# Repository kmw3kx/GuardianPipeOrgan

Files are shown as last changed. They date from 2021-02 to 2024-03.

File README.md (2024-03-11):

# GuardianPipeOrgan

[Terrako by rongs1234 on DeviantArt](https://www.google.com/url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)

## Table of Contents
- [README Requirements](#readme-requirements)
- [Project Pre-Planning](#project-pre-planning)
- [Materials used](#materials-used)
- [Wiring](#wiring)
- [Pseudocode](#pseudocode)
- [Working on the Code](#working-on-the-code)
- [CAD](#cad)
- [Schedule](#schedule)
- [What went wrong](#what-went-wrong)

### README Requirements

<details>
        
        Knock out the design completely in CAD before you start construction.  Leave room for wires.

        Throughout the project, document your work on github.  You should communicate enough information so that someone else in your class could reasonably replicate your project.

        You should include, in this order:

        Description of the planning that went into the project, design decisions, and engineering details
        Materials used
        Wiring diagram of your circuit
        Commented code
        CAD renderings
        Actual photos and/or video (well lit and in focus)
        Your process or a schedule of how you spent your time
        Discussion of problems, errors, miscalculations, and missteps and how you overcame them
        If you didn't finish, please add an obituary, detailing what you'd do if you picked this project back up, and anything you'd have done differently.
        
</details>

### Project Pre-Planning

1. *Create your question:*

  a. *What's the problem you're trying to solve?*

    i. Have a robot that can serenade people with beautiful music
    
    ii. Build a self-playing organ
    
  b. *How will you determine if you've solved your problem? (make sure your problem is specific and testable!)*
  
    i. We can play Zelda's lullaby on it and have it sound pure, and at a constant volume. Is a midi output so that it can also play other songs
    
2. *Break down your problem:*

  a. **Criteria (goals):**
  
    i. *How does it solve the problem?*
    
      1.
      
    ii. *~~What should it look like:~~*
    
    iii. *What is it going to do?*
    
  b. **Constraints (limitations)**
  
    i. *Don't hurt anyone*
    
      1. Pressurized Air can be dangerous
      
    ii. *Budget:*
    
      1. I think we can get by with $50
      
    iii. *Time frame* (roughly 2 months)
    
    iv. *Size* (laser cutter: 300mm x 600mm , 3d Printer 8&quot;x8&quot;x9&quot;)
    
      1. The size that the pipes will need to be
      
    v. *Any knowledge limitations that you'll need to correct?*
    
      1. Pneumatics
      
      2. How to design a valve
      
      3. Controlling multiple solenoids with not many pins
      
      4. Flow rate
      
      5. MIDI Input/Output
      
      6. Organ Pipe design
      
3. *Research:*

  a. *Delegate this with your partner! Whose researching what?*
  
    i. Let's make separate Google Docs to take notes in about each topic
    
      1. Bob = MIDI, Using a microcontroller as a MIDI in/out
      
      2. Justyn = Flow rate, pneumatics, fluid dynamics
      
      3. Both: Organ Pipe Design
      
        a. Hopefully getting in touch with an organ manufacturer up in Staunton
        
  b. *Improve your google-jitsu.*
  
  c. *Remember, you DON'T have a plan yet. This is research for pre-planning. Researching mp3 shields….how does a piezo buzzer work, that sort of thing…WHAT IS PID?? How do I determine CoM in Onshape?*
  
  4. I cannot tell you what questions to ask, as they should be very project specific, but for example, you might want to know how an organ pipe works before building an organ, or you might want to know how to calculate wheel speed , before you build a PID box that controls wheel speed.

4. *Make a list of possible solutions:*

  1. *Whats it going to look like?*

  3. *What components will it use?*

    1. Arduino or Circuit Python
    
  4. *How does this solution solve the problem?*

  6. **Make sure to include a short list of pros and cons for each solution.**

  8.

1. We are pretty decided that it's going to be an organ
2. Solenoids or Solenoid Valves?

  1. Solenoids

    1. Pros: Cheaper, less specialized, have been used before for this type of project

    2. Cons: The solenoid valves are gonna be more precise and a better seal
    
  2. Solenoid valves

    1. Pros
3.

[Link to engineering design process:](https://www.teachengineering.org/design/designprocess)

[Link](https://docs.google.com/document/d/1uND1lurYmUpj-_9FQsYxZuwOPflugXZLaDDHEH4wFzs/edit?usp=sharing)

### Materials used
* 32 Valves (laser-cut casing, [3/16" ID x 5/16" OD silicone tubing](https://www.amazon.com/dp/B07TH8H1QP/ref=cm_sw_em_r_mt_dp_J0TEWZFQ2DN48WCQM4QV?_encoding=UTF8&psc=1), and 3D printed cam)
* 32 3D printed Organ Pipes 
* Arduino Mega (from Dr. Shields)
* [MIDI 5-pin to USB-A Cable](https://www.amazon.com/dp/B087G7L7J2/ref=cm_sw_em_r_mt_dp_3BY1T0T89K53A4C2TZDT?_encoding=UTF8&psc=1)
* [MIDI connector](https://www.amazon.com/dp/B07NY6Z2N7/ref=cm_sw_em_r_mt_dp_BFAF0GJ7GPHXVVTXCVRJ?_encoding=UTF8&psc=1)
* 220 Ohm 1/4watt resistor (In Sigma Lab)
* [1N4148 diode](https://www.amazon.com/dp/B06XB1R2NK/ref=cm_sw_em_r_mt_dp_FQDK5978XHRZRAK23W6Y) (I had one on hand, but I included a link to order one as well)
* 10k Ohm 1/4watt resistor (In Sigma Lab)
* 470 Ohm 1/4watt resistor (I used 2x220 instead)
* [6N138 optocoupler](https://www.amazon.com/dp/B07DLTSXC1/ref=cm_sw_em_r_mt_dp_HDJK9QW9ZMRRCRK7CJNF?_encoding=UTF8&psc=1)
* Balloons!
* Lots of bolts and screws
* Breadboard
* wires

### Wiring

[MIDI Fritzing file](Wiring/MidiCircuit.fzz)

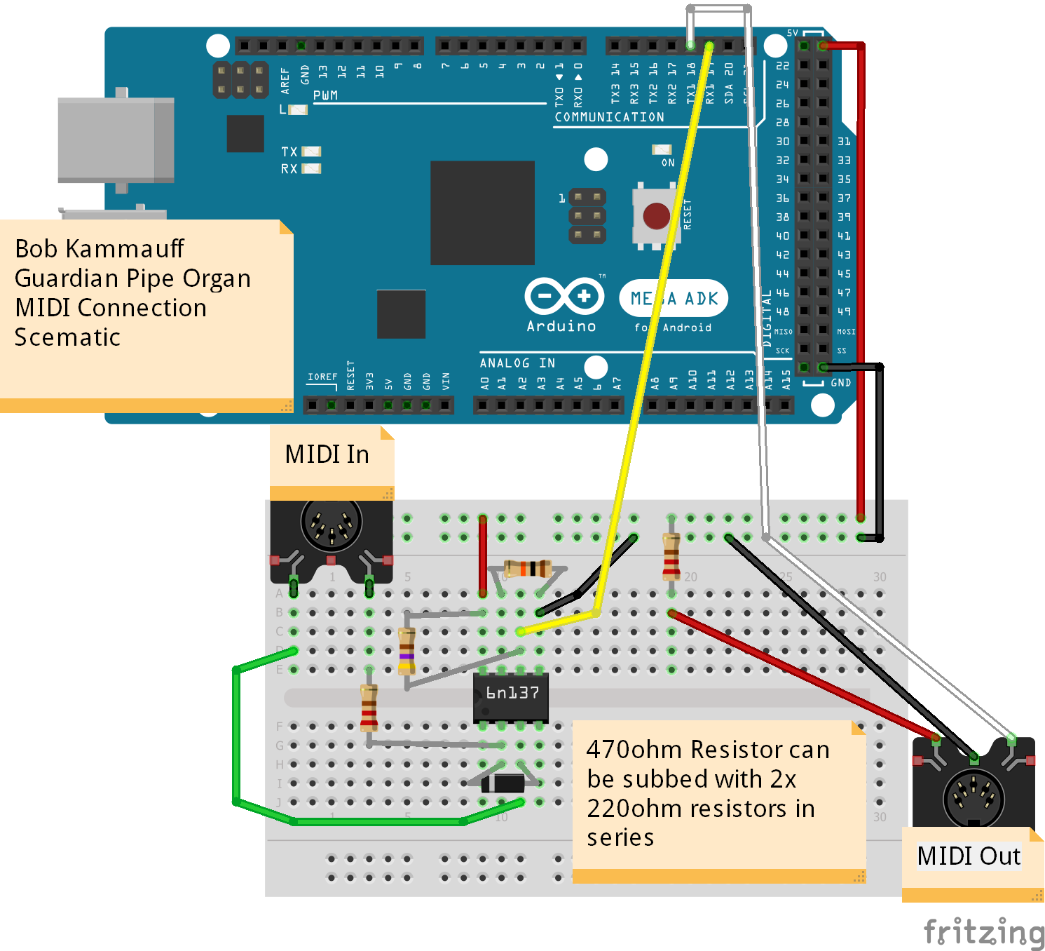
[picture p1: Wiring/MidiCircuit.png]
[](Wiring/MidiCircuit.png)

### Pseudocode
Link to code [here.](GuardianPipeOrganOutPseudoCode)

<details>
        
        ```python
        # Bob Kammauff
        # 2/4/2021
        # Guardian Pipe Organ - Output
        # pseudocode

        # at the top here, put all of the libraries we'll be using

        import time

        import digitalio
        import touchio
        import busio
        import board
        import usb_midi
        import neopixel

        import adafruit_midi

        from adafruit_midi.note_on          import NoteOn
        from adafruit_midi.control_change   import ControlChange
        from adafruit_midi.pitch_bend       import PitchBend

        # + some others that I don't know about

        # set up any serial port communication we'll need

        # using some type of shift register or port thingy to get more pins
        # so initialize that

        # Read any incoming MIDI messages (events) over USB
        # looking for note on, note off messages

        # Our organ will have 32 notes starting at middle C (C4) and going up to G6
        # Each time a note on value is detected, write the pin connected to that note's solonoid high
        # Each time theres a note off value, write the pin low

        # there will be transistors in between every solonoid to supply the correct voltage
        ```
   
</details>

## Working on the Code

Throughout this process, I gradually moved from using multiple metro expresses, to using a metro and an Arduino Mega, to using just the mega. So a lot of what I've written is very specific to the point in time when I was using a metro M0. If you want to read that stuff, I'll include it all into a expanding section:

It's not required for the rest of the README to make sense

<details>

So, I do not have the transistors or the shift registers or any of that fancy stuff yet; all I got is a Circuit Python and some LED's, but the coding will be the same either way. Let's set up a circuit python to read Midi Data coming from my computer to light up some led's.

The wiring is easy. a bunch of LED's and resistors. Iet's get working on the code for it.

Ok so I've already run into a couple problems about how to write the code. The code I'm taking it from sets all of the pins using a for loop. But, I can't find a way to do that with digital pins because they require a 2nd initialization to tell the pin whether to be input or output. Brute forcing it might just be the correct solution, but the idea of having the pins in an array just makes the code so much simpler.

Now that I've described the problem, the solution seems clear: do a mix

This didn't work
        
```python
pins = [board.D13,
        board.D12,
        board.D11,
        board.D10,
        board.D9,
        board.D8,
        board.D7,
        board.D6,
        board.D5,
        board.D4,
        board.D3,
        board.D2]

# add LED's
# ledG = digitalio.DigitalInOut(board.D1)
# ledG.direction = digitalio.Direction.OUTPUT
# n
# or do it like this

noteLEDs = []
x = 0
for pin in pins:
    noteLEDs = [digitalio.DigitalInOut(pin)]
    print(str(pin))

del pins, x  # done with that
noteLEDs.direction = digitalio.Direction.OUTPUT
```

Lets try this now: set the pins each to a variable, then set each variable to a list.

```python
pinD13 = digitalio.DigitalInOut(board.D13)
pinD12 = digitalio.DigitalInOut(board.D12)
pinD11 = digitalio.DigitalInOut(board.D11)
pinD10 = digitalio.DigitalInOut(board.D10)
pinD9 = digitalio.DigitalInOut(board.D9)
pinD8 = digitalio.DigitalInOut(board.D8)
pinD7 = digitalio.DigitalInOut(board.D7)
pinD6 = digitalio.DigitalInOut(board.D6)
pinD5 = digitalio.DigitalInOut(board.D5)
pinD4 = digitalio.DigitalInOut(board.D4)
pinD3 = digitalio.DigitalInOut(board.D3)
pinD2 = digitalio.DigitalInOut(board.D2)

pinD13.direction = digitalio.Direction.OUTPUT
pinD12.direction = digitalio.Direction.OUTPUT
pinD11.direction = digitalio.Direction.OUTPUT
pinD10.direction = digitalio.Direction.OUTPUT
pinD9.direction = digitalio.Direction.OUTPUT
pinD8.direction = digitalio.Direction.OUTPUT
pinD7.direction = digitalio.Direction.OUTPUT
pinD6.direction = digitalio.Direction.OUTPUT
pinD5.direction = digitalio.Direction.OUTPUT
pinD4.direction = digitalio.Direction.OUTPUT
pinD3.direction = digitalio.Direction.OUTPUT
pinD2.direction = digitalio.Direction.OUTPUT

noteLEDs = [pinD13,
            pinD12,
            pinD11,
            pinD10,
            pinD9,
            pinD8,
            pinD7,
            pinD6,
            pinD5,
            pinD4,
            pinD3,
            pinD2]

# Brute forced
```
</details>

Anyway, here's my thought process simplified:

After trying to get serial communication working with a metro express and failing for a week, I decided to totally ditch using one and instead use just an arduino mega to process MIDI data and control all of the servos. 

This means that instead of being able to send midi data just across the usb cable like with the metro, I actually had to go and order a MIDI to USB cable from Amazon. [Here's](https://www.amazon.com/dp/B087G7L7J2/ref=cm_sw_em_r_mt_dp_3BY1T0T89K53A4C2TZDT?_encoding=UTF8&psc=1) the one I ended up buying.

I guess I should explain my goals for this code:

1. Connect the arduino mega to the 32 servos that control the valves
2. Receive data being transmitted over the MIDI IN jack hooked up to the computer
3. process that data to get what note should be either turned on or off
4. send the corresponding command to the servo, allowing air to pass, and make the organ pipe speak.

[Here's](https://github.com/jkammau97/GuardianPipeOrgan/blob/8430313b24fd7d28eb77173dfa6983c463fdca4e/Arduino%20Code/GuardianPipeOrganV1/GuardianPipeOrganV1.ino) the code I came up with for the servos:

<details>
        ```arduino
        
        /*
          Bob Kammauff & Justyn Reyes
          Midi Output - Guardian Pipe Organ
          3/25
          Last Updated: 5/24/2021
        */

        #include <Servo.h>
        #include <stdio.h>
        #include <string.h>

        #define NUM_NOTES 32
        #define FIRST_PIN 22
        Servo servos[NUM_NOTES];

        #define OFF_ANGLE 0
        #define ON_ANGLE 180

        #define FIRST_NOTE 53 //corresponds to F3
        #define LAST_NOTE 84 //corresponds to C6

        //If input falls outside this range, data gets thrown out

        int note, velocity;

        String fromSerial;

        char input[10];

        int incomingByte = 0; // for incoming serial data

        void setup() {
          // put your setup code here, to run once:
          Serial.begin(9600); //For communicating with the computer

          for (int i = 0; i < NUM_NOTES; i++)
          {
            servos[i].attach(i + FIRST_PIN);

            Serial.print("Servo ");
            Serial.print(i);
            Serial.print(" attached to pin ");
            Serial.println(i + FIRST_PIN);
            servos[i].write(OFF_ANGLE);

          }
          Serial.println("All Servos Attached");

          for (int n = 0; n < NUM_NOTES; n++)
          {
            Serial.print("Testing servo ");
            Serial.println(n);
            servos[n].write(ON_ANGLE);
            delay(100);
            servos[n].write(OFF_ANGLE);
            delay(50);
          }

          Serial.println("Done");
        }

        void loop() {
          // put your main code here, to run repeatedly:
          // send data only when you receive data:
          while (Serial.available() > 0)
          {
            fromSerial = Serial.readStringUntil('\n');
            Serial.println(fromSerial); //Echoes back what was received
            fromSerial.toCharArray(input, fromSerial.length());
            // Returns first token
            char *token = strtok(input, " ");
            note = atoi(token);
            token = strtok(NULL, " ");
            velocity = atoi(token);
            // Keep printing tokens while one of the
            // delimiters present in str[].
            if (note >= FIRST_NOTE and note <= LAST_NOTE) //If note is in range
            {
              Serial.print("Note is: ");
              Serial.println(note, DEC);
              Serial.print("Vel is: ");
              Serial.println(velocity, DEC);
              if (velocity > 0)
              {
                servos[note - FIRST_NOTE].write(ON_ANGLE);
              } else
              {
                servos[note - FIRST_NOTE].write(OFF_ANGLE);
              }

            }

          }
        }
        
        ```
</details>

This code simply establishes communication with the servos, and ties each one to a note. In MIDI, each note on the keyboard is assigned a name and an integer corresponing to said note, and then the next part of the data packet the midi sends over is called velocity, which is simply how loud the note should be played. I'll include some specifics about how a midi byte is transferred in the section about the midi code, but for now, all you need to know is that midi data simply sends over a note and whether to turn it on or off at the time when it is sent. So, back when I had no access to said midi data, I made up my own and simply sent it over the serial monitor from my computer. The syntax for said data is: note integer, space, velocity integer(anything that wasn't zero turned it on, with zero turning it off), and another space. My code takes that data, splits it via the spaces, and then converts the text of the numbers into actual integer values that it can use in calculations. These values are then echoed back over the serial monitor, and the corresponding servo makes the correct movement. 
        
Now, for the MIDI code that reads the data coming over the ports! [Here](Arduino Code/ReceiveMidiWEdits/ReceiveMidiWEdits.ino) it is!

I'm actually going to wait to put it in the README for now. It needs a LOT of polishing up, but this is the source that I got it from, and where I'm going to continue to work on this code
        
This code DOES work and it works consistently, but it's not giving me the data that I was expecting it to. It's like a geode; the gem I'm looking for is in there, but it's gonna take some parsing to extract it into a useable chunk. instead of giving me `command, note, velocity` like I was expecting, it's giving me: `Command byte, 255, 255, Note byte, 255, 255, Velocity byte, 255, 255`

### CAD

[Link to Onshape](https://cvilleschools.onshape.com/documents/e358e4e3ba9e07c5ae938246/w/c6c09eac29318e33af1bc1ef/e/29cbd6e08dd43a0f8d613074)
        
The majority of this project was spent in CAD HELL. Trying to make a 3D object that converts air into sound is challenging to get right. What I first ended up doing was researching how Pipe organ pipes make sound and what kind of geometry creates said conditions. 
        
I'm especially proud of my design for the pipes. They are stopped organ pipes with caps to adjust the tuning. Stopping the organ pipes drops the octave and requires less air pressure to sound, allowing for them to be more practical in my design. They are as thin walled as i could 3D print. 
        
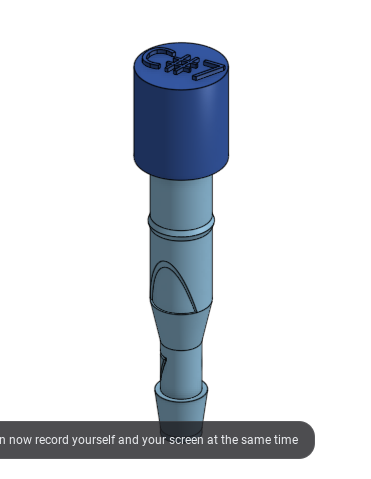
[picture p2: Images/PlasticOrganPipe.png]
[](Images/PlasticOrganPipe.png)
        
I filled in the space under the top lip to allow these organ pipes to be able to be printed with no supports! Carefully follow the slope and cut it off with a razor blade and it should work perfectly. Be careful with the bottom lip; if it gets too mangled, it might not direct air towards the upper lip and the organ pipe won't sound.
        
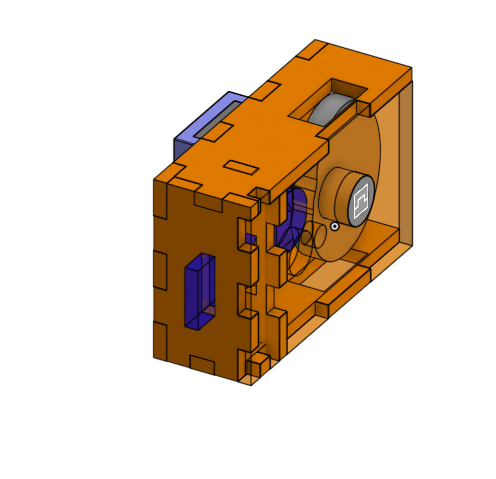
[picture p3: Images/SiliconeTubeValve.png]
[](Images/SiliconeTubeValve.png)

I am also very proud of the valve design. They use silicone tubing and a mini servo in a cam and follower mechanism to stop air flow electronically, much cheaper than a solenoid valve. The design is not my own (I can't find the original inspiration, sadly), but I did increase the size to accomodate a higher volume of air.

### Schedule

| 1st week |  Get midi working with the circuit pythons  |  Feb. 22nd-26th |
|:---:|:---:|:---:|
| 2nd week | Order all of the parts we’ll need | Mar. 1st-5th |
| 3rd week | Design the organ pipes and the valve system | Mar. 8th-12th |
| 4th week | Design the Shell to put the organ into | Mar. 15th-19th  |
| 5th week | Fabrication | Mar.22nd-26th |
| 6th week | Troubleshooting (buffer week) | Mar. 29th-Apr.2 |

#### 3rd Week

Bob Goal: Finish the design for the organ pipes. Design the Valve system.

Justyn Goal: Fix up the github, Add pictures, cad, toc. Lay out the valves once Bob Has made the valves

Evaluation: Bob really had trouble delegating work, so we only achieved designing the valve system. We finally our 3D printed Whistle prototype and that has caused us to reevaluate the design of our organ. Instead of using open flue organ pipes, we are going to use closed organ flue pipes, because they allow for a lower tone in a smaller size, and require less air pressure. And we are going to do pipes C5-G7 so they are smaller yet (longest one is 1/2 a foot!) Since they are now smaller, the silicone tubing of 1/4" might be too big now, which means we'll have to redesign the valve to fit the new size of tubing.

#### 4th Week
Justyn: Design the Organ pipes to make them stopped and tune-able by adjusting the screw on stopper. Add nozzle on the bottom to directly friction fit connect the tubes to. add brackets to the design of the organ pipes to hold them upright

Bob: Work on code; Get Servos working with midi and arduino mega.

3/17/2021

Justyn is having computer problems so I'm the only one who can do Onshape. I had to really think about how big everything was going to be, so I had to scale it down to the bottom note of F4 instead of C5. Really, I just couldn't realistically fabrcate pipes smaller than that C7 stopped pipe. I added threads on to both the cap and the top of the pipe so that the pipes can be tuned relatively easily. Hopefully. Next course of action is to define the silicone tubing size again and then remake the valve so it is smaller. Lot's of redesigning, but it will all work out.

#### 5th Week

Ok so thankfully, at the time I am writing this, my life has just gotten way less busy. All of my music stuff is done, so it's time to focus on school again. But we're also super behind on schedule. Today, I just realized that there was an extremely simple solution to this project: buy a cheap melodica and put it in the guardian. Unfortunately, we're already so deep into the organ pipes that it's pointless to just start from scratch, and besides; I prefer the flute tone of the pipes instead of the reedy tone of te melodica. That, and that the melodica wouldn't fit nicely in the robot. but that's an easy idea to save for the future!

This week, Bob is on code, and Justyn is on CAD. Thankfully, I think most of the code for the arduino mega is already on the internet so I can just borrow it. But first, we need to establish a tubing size, and then 

### What Went Wrong

Why will I be unable to finish this project by the end of the year? A few reasons:

1. Lack of In-Person Lab time with my partner
2. Long turn-around on fabrication
3. The project is just insane

#### 1. Lack of In-Person Lab time with my partner

Never being able to actually see my partner face to face makes it extremely difficult to collaborate. I would try to delegate work for him to do but not being able to see him doing it and making sure he stayed on track meant that I would ultimately be the one doing it. Me also being the only one to understand the physics of sound and midi also meant it was challenging to convey what I wanted. 

I could fix this in the future by not choosing such a complicated project to do during a national pandemic. Also I started to remedy the problem by coming in on my virtual days when we started having school in person. 

#### 2. Long turn-around on fabrication

This started with me 3D printing the first test whistle. It easily took 2 weeks from submitting the file for printing to actually get it into my hands so I could test it. That day I learned the hard lesson to never print a closed cyllender. To quote my teach: 
> "closed or nearly closed cylinders are nightmares, filled with monsters and support material that wont dissolve."

This was just the starting point of design hell. Trying to print something that makes sound is incredibly difficult, because you just can't see how it will sound in CAD; you have to print it out and test it.

Thankfully I did my research and found out how whistles make noise so there was less of that, but I still had to print out 5 separate pipes before one of them actually worked. When ur not in the lab 5 days a week, it just increases the turn-around time as it would have to dissolve in the bath for at least a day after printing

The circumstances aren't just to blame; I also had to learn how to design parts that would use no support material. I did a good job with it tho, cuz my parts are now real nice.

#### 3. The project is just insane

When I was first pitching it to my teacher, he thought I just wanted to make a robot play music, so he suggested that I just use a MP3 shield and call it a day 

**Oh how easy that would've been...**

MIDI-Controlled Pipe Organs are just so cool. Something about bringing the perfection of MIDI into the physical world just sounds so cool when you hear it. But it's also just unlike anything anyone else here has tried to do, so I have to build it from the ground up. Thankfully there are projects online that are quite similar, but I was still just trying to figure out the best way to do it only a month ago. 

        I hope to revisit this project someday, but for the time being, it'll have to wait.

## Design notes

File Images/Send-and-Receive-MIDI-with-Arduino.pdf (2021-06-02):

## http://www.instructables.com/id/Send-and-Receive-MIDI-with-Arduino/

Food (http://www.instructables.com/tag/type-id/category-food/) Living (http://www.instructables.com/tag/type-id/category-living/) Outside (http://www.instructables.com/tag/type-id/category-outside/) | Play (http://www.instructables.com/tag/type-id/category-play/) | Technology (http://www.instructables.com/tag/type-id/category-technology/) Workshop (http://www.instructables.com/tag/type-id/category-workshop/)

# Send and Receive MIDI with Arduino

by amandaghassaei (http://www.instructables.com/member/amandaghassaei/?utm_source=pdf&utm_campaign=title) on June 9, 2012

## Table of Contents

## Author:amandaghassaei amandaghassaei.com Currently working for instructables!

# Intro: Send and Receive MIDI with Arduino

This instructable will show you how to use an Arduino to send and receive a variety of MIDI messages so you can start building your own MIDI controllers and instruments. First I'll talk a little bit about MIDI protocol, if you're just looking for sample code skip ahead to steps 5-9.

If you know absolutely nothing about MIDI note, velocity, and pitchbend or are confused about what MIDI does and why you would want to use it, check out my What is MIDI? (http://www.instructables.com/id/What-is-MIDI/) instructable.

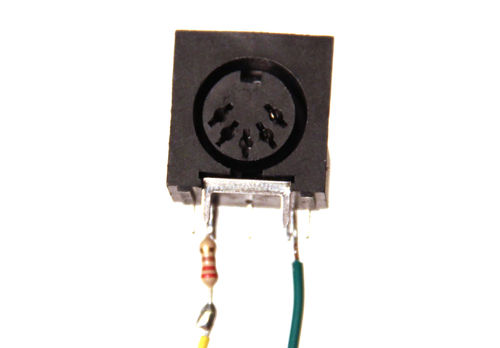
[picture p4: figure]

# Step 1: Bytes and Bits

To understand MIDI communication, you have to understand a little about bytes and bits. A byte is a packet of data used to store information. In MIDI protocol, each byte

## is made up of 8 bits; bits can only equal to 0 or 1. A sample byte is given below:

11010111

Each 1 or 0 in this byte is a bit. The leftmost bit is called the most significant bit (or MSB) and the rightmost bit is called the least significant bit (or LSB).

Bytes of the form above are binary numbers because they are expressed using only 1's and 0's. We can convert this number to base ten as well:

## 11010111 in binary (base 2) = 215 in decimal (base 10)

If you need help converting numbers from binary to decimal or vice versa check out Wolfram Alpha (http://www.wolframalpha.com/) . Type in a binary number followed with "from binary to decimal" to get the decimal equivalent. Wolfram Alpha is also great for converting to and from hexadecimal (http://en.wikipedia.org/wiki/Hexadecimal) .

Wikipedia is a good resource for more information about bytes (http://en.wikipedia.org/wiki/Byte) and binary (http://en.wikipedia.org/wiki/Binary_numeral_system) .

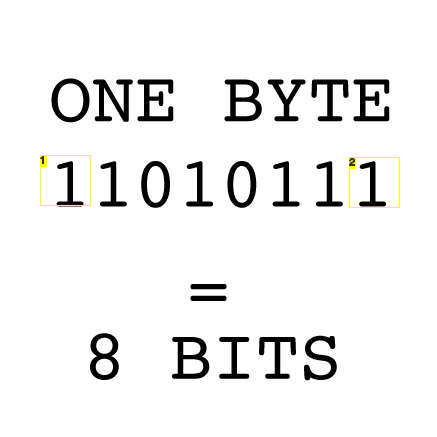
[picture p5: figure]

## Image Notes 1. most significant bit (MSB) 2. least significant bit (LSB)

# Step 2: A Bit About MIDI Protocol

A really basic overview of MIDI terms and concepts is given here (http://www.instructables.com/id/What-is-MIDI/) .

MIDI messages are comprised of two components: commands and data bytes. The command byte tells the MIDI instrument what type of message is being sent and the subsequent data byte(s) store the actual data. For example a command byte might tell a MIDI instrument that it going to send information about pitchbend, and the data byte describes how much pitchbend and which note to pitchbend.

MIDI data bytes range from 0 to 127. Convert these numbers to binary and we see they range from 00000000 to 01111111, the important thing to notice here is that they always start with a 0 as the most significant bit (MSB). MIDI command bytes range from 128 to 255, or 1000000 to 11111111 in binary. Unlike data bytes, MIDI command bytes always start with a 1 as the MSB. This MSB is how a MIDI instrument differentiates between a command byte and a data byte.

## MIDI commands are further broken down by the following system:

The first half of the MIDI command byte (the three bits following the MSB) sets the type of command. More info about the meaning on each of these commands is here (http://www.instructables.com/id/What-is-MIDI/) .

## 10000000 = note off 10010000 = note on 10100000 = aftertouch 10110000 = continuous controller 11000000 = patch change 11010000 = channel pressure 11100000 = pitch bend 11110000 = non-musical commands

The last half of the command byte sets the MIDI channel. All the bytes listed above would be in channel 0, command bytes ending in 0001 would be for MIDI channel 1, and so on.

All MIDI messages start with a command byte, some messages contain one data byte, others contain two or more (see image above). For example, a note on command byte is followed by two data bytes: note and velocity.

I'm going to explain how to use note on, note off, velocity, and pitchbend in this instructable, since these are the most commonly used commands. I'm sure you will be able to infer how to set up the others by the end of this.

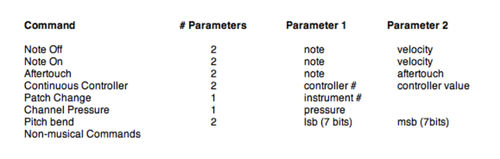
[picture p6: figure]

# Step 3: Send MIDI Messages with Arduino- Hardware

## Parts List:

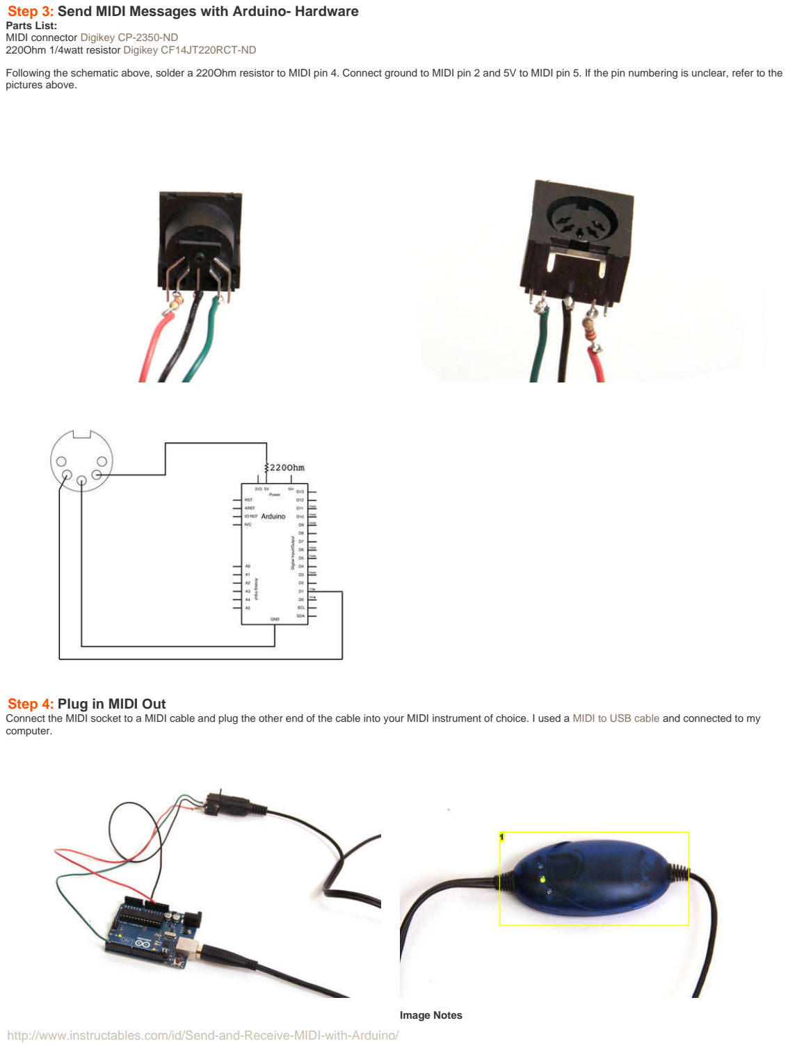
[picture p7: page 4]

MIDI connector Digikey CP-2350-ND (http://www.digikey.com/product-detail/en/SDS-50J/CP-2350-ND/97033)
220Ohm 1/4watt resistor Digikey CF14JT220RCT-ND (http://www.digikey.com/product-detail/en/CF14JT220R/CF14JT220RCT-ND/1830334)

Following the schematic above, solder a 220Ohm resistor to MIDI pin 4. Connect ground to MIDI pin 2 and 5V to MIDI pin 5. If the pin numbering is unclear, refer to the pictures above.

# Step 4: Plug in MIDI Out

Connect the MIDI socket to a MIDI cable and plug the other end of the cable into your MIDI instrument of choice. I used a MIDI to USB cable (http://www.amazon.com/Cable-Converter-Music-Keyboard-Window/dp/B0017H4EBG) and connected to my computer.

## Image Notes

## 1. MIDI to usb

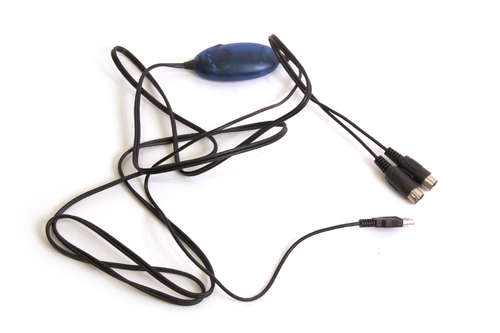
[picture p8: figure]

# Step 5: Basic Note On, Note Off with Arduino

This code sends MIDI messages out arduino digital pin 1 using note on and note off commands.

## As I explained in step 3, the MIDI commands for note on and note off are as follows: noteON = 10010000 = 144 noteOFF = 10000000 = 128

Both of these commands are followed by two more bytes to make a complete MIDI message, the first is note and the second is velocity (for more info about what "note" and "velocity" mean check out my introductory MIDI instructable). Note and velocity can range from 0 to 127. In this example I used notes ranging from 50 to 69 (D3 to A4):

## for (int note=50;note<70;note++){} and I set the velocity to 100:

int velocity = 100;

So when the function MIDImessage() is called in the loop() of the arduino sketch, it sends the three bytes: Serial.write(command);
Serial.write(MIDInote);
Serial.write(MIDIvelocity);
if the "command" in the MIDImessage() function is noteON then the note will start, if it is noteOFF the note will stop.

The code below plays the notes D3-A4 in a loop, it turns on a MIDI note for 300ms then wait 200ms before turning on the next note. I wrote a MaxMSP (http://cycling74.com/downloads/) patch (you can download the runtime version for free) that displays the incoming MIDI messages and attached it below. Here is an example video:

/*
MIDI On/Off Messages
By Amanda Ghassaei
July 2012
http://www.instructables.com/id/Send-and-Receive-MIDI-with-Arduino/

* This program is free software; you can redistribute it and/or modify * it under the terms of the GNU General Public License as published by * the Free Software Foundation; either version 3 of the License, or * (at your option) any later version.

*/

int vel = 100;//velocity of MIDI notes, must be between 0 and 127 //higher velocity usually makes MIDI instruments louder

int noteON = 144;//144 = 1001000 in binary, note on command
int noteOFF = 128;//128 = 10000000 in binary, note off command

void setup() {
// Set MIDI baud rate:
Serial.begin(31250);
}

void loop() {
for (int note=50;note<70;note++) {//from note 50 (D3) to note 69 (A4) MIDInoteON(note, vel);//turn note on
delay(300);//hold note for 300ms
MIDInoteOFF(note, vel);//turn note off
delay(200);//wait 200ms until triggering next note }
}

//send MIDI message- turn note on
void MIDInoteON(int pitch, int velocity) { Serial.write(noteON);//send note on command Serial.write(pitch);//send pitch data Serial.write(velocity);//send velocity data }

//send MIDI message- turn note off
void MIDInoteOFF(int pitch, int velocity) { Serial.write(noteOFF);//send note off command Serial.write(pitch);//send pitch data Serial.write(velocity);//send velocity data }

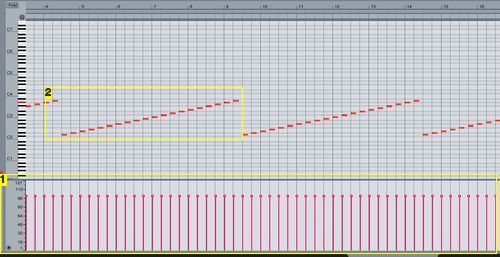
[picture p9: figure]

## Image Notes 1. velocity set to constant 100 2. 20 notes, increasing by one semitone, with .3s duration

## File Downloads

midiin.maxpat.zip (http://www.instructables.com/files/orig/FK2/FFFM/H673DC2U/FK2FFFMH673DC2U.zip) (1 KB)
[NOTE: When saving, if you see .tmp as the file ext, rename it to 'midiin.maxpat.zip'] (http://www.instructables.com/files/orig/FK2/FFFM/H673DC2U/FK2FFFMH673DC2U.zip)

# Step 6: Note Off with 0 Velocity

You may have noticed in the previous step's video, that the velocity appeared to set back to 0 when the note off message was sent. This is because a MIDI message with a note on command and velocity 0 is the same as a note off message. Sometimes when a software MIDI environment receives a note off message it will automatically translate it into a note on message with velocity 0 because they are the same. You will probably find that it is easier to program MIDI by sending these note on/velocity=0 messages rather than sending note off.

The code below does the exact same thing as the code in the last step, but it only uses note on commands. Essentially, I've replaced the following line: MIDImessage(noteOFF, note, velocity);

## with:

MIDImessage(noteON, note, 0);

/*
MIDI On Messages with 0 velocity
By Amanda Ghassaei
July 2012
http://www.instructables.com/id/Send-and-Receive-MIDI-with-Arduino/

* This program is free software; you can redistribute it and/or modify * it under the terms of the GNU General Public License as published by * the Free Software Foundation; either version 3 of the License, or * (at your option) any later version.

*/

int velocity = 100;//velocity of MIDI notes, must be between 0 and 127 //(higher velocity usually makes MIDI instruments louder)

int noteON = 144;//144 = 1001000 in binary, note on command

void setup() {
// Set MIDI baud rate:
Serial.begin(31250);
}

void loop() {
for (int note=50;note<70;note++) {//from note 50 (D3) to note 69 (A4) MIDImessage(noteON, note, velocity);//turn note on delay(300);//hold note for 300ms
MIDImessage(noteON, note, 0);//turn note off
delay(200);//wait 200ms until triggering next note }
}

//send MIDI message
void MIDImessage(int command, int MIDInote, int MIDIvelocity) { Serial.write(command);//send note on or note off command Serial.write(MIDInote);//send pitch data Serial.write(MIDIvelocity);//send velocity data
}

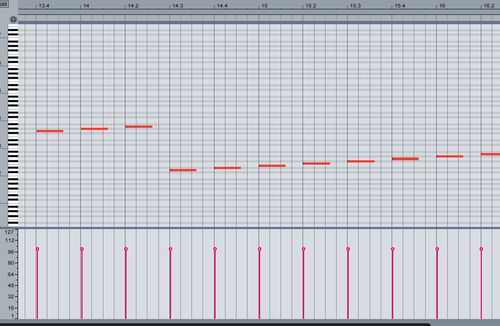
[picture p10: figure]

# Step 7: Variable Velocity and Arduino

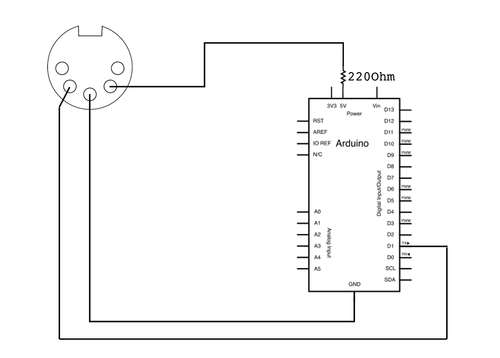
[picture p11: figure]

In this code I've modified the variable velocity so that it increases with increasing note number. In the beginning of the loop() function the variable velocity is set to 20,

## then it is increased by five in each iteration of the for loop:

velocity += 5;
so for note = 50, velocity = 20, then for note = 51, velocity = 25, then for note = 52, velocity = 30... and so on.
once the end of the loop() function is reached, the velocity is reset back to 20.

Here's a video of the end result, notice how the volume increases with increasing velocity.

/*
MIDI note on messages with variable velocity
By Amanda Ghassaei
July 2012
http://www.instructables.com/id/Send-and-Receive-MIDI-with-Arduino/

* This program is free software; you can redistribute it and/or modify * it under the terms of the GNU General Public License as published by * the Free Software Foundation; either version 3 of the License, or * (at your option) any later version.

*/

int noteON = 144;//144 = 1001000 in binary, note on command

void setup() {
// Set MIDI baud rate:
Serial.begin(31250);
}

void loop() {
int velocity = 20;//set velocity to 20
for (int note=50;note<70;note++) {//from note 50 (D3) to note 69 (A4) MIDImessage(noteON, note, velocity);//turn note on delay(300);//hold note for 300ms
MIDImessage(noteON, note, 0);//turn note off
delay(200);//wait 200ms until triggering next note velocity += 5;//ad 5 to current velocity value
}

//send MIDI message
void MIDImessage(int command, int MIDInote, int MIDIvelocity) {

Serial.write(command);//send note on or note off command Serial.write(MIDInote);//send pitch data Serial.write(MIDIvelocity);//send velocity data

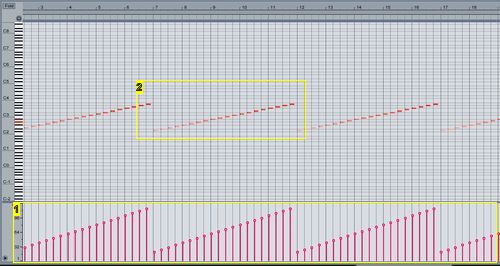
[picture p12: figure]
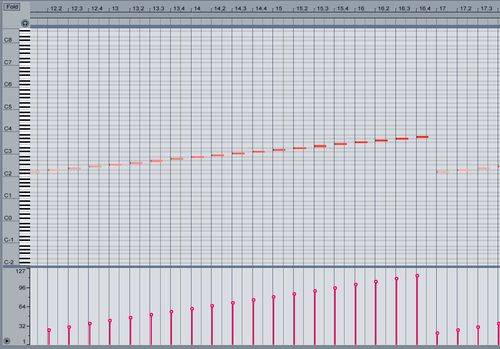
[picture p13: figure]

## Image Notes 1. velocity increases by 5 2. 20 notes, increasing by one semitone, duration of 0.3s

# Step 8: Pitchbend and Arduino

Now that you know how to control note on and note off, you can try pitchbend.

Pitchbend information is stored in 2 data bytes, and most significant byte (MSB) and a least significant byte (LSB). Each of these bytes contains only 7 bits of information. This means that all pitchbend information is stored in 14 bits, with the most significant 7 bits stored in the MSB and the least significant 7 bits stored in the LSB.

For most applications you will only find yourself changing pitchbend via the MSB and just setting the LSB to 0. In this case you have 7 bits of resolution for pitchbend (128 steps). In MIDI protocol pitchbend = 64 is no pitchbend, pitchbend greater than 64 is pitchbends the frequency up, and less than 64 pitchbends the frequency down.

In the example below a note played and held, then played again while the pitchbend increments from 64 to its max value of 127, then played a third time while the pitchbend increments from 64 to its min value of 0. This sequence is looped forever. The images above show the output in ableton from this Arduino sketch.

/*
MIDI Pitchbend (msb)
By Amanda Ghassaei
July 2012
http://www.instructables.com/id/Send-and-Receive-MIDI-with-Arduino/

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

*/

int noteON = 144;//144 = 1001000 in binary, note on command
//noteON data storage:
int note = 60;//middle c
int velocity = 100;//velocity of MIDI notes, must be between 0 and 127 //(higher velocity usually makes MIDI instruments louder)

int pitchbend = 224;//224 = 11100000 in binary, pitchbend command //pitchbend data storage:
int lsb = 0;//least siginificant bit of pitchbend message
int msb = 0;//most significant bit of pitchbend message

void setup() {
// Set MIDI baud rate:
Serial.begin(31250);

void loop() {
//first play note w/o pitchbend
MIDImessage(pitchbend, 0, 64);//reset pitchbend to 0 (zero pitchbend is lsb = 0, msb = 64) MIDImessage(noteON, note, velocity);//turn note on
delay(700);//sustain note
MIDImessage(noteON, note, 0);//turn note off
delay(500);//wait 500ms until triggering next note

//then play with pitchbend up
MIDImessage(pitchbend, 0, 64);//reset pitchbend to 0 (zero pitchbend is lsb = 0, msb = 64) MIDImessage(noteON, note, velocity);//turn note on
for (msb=64;msb<=127;msb++){//increase pitchbend msb 64 (no pitchbend) to 127 MIDImessage(pitchbend, lsb, msb);//send pitchbend message
delay(10);
}
MIDImessage(noteON, note, 0);//turn note off
delay(500);//wait 500ms until triggering next note

//then play with pitchbend down
MIDImessage(pitchbend, 0, 64);//reset pitchbend to 0 (zero pitchbend is lsb = 0, msb = 64) MIDImessage(noteON, note, velocity);//turn note on
for (msb=64;msb>=0;msb--){//decrease pitchbend msb from 64 (no pitchbend) to 0; MIDImessage(pitchbend, lsb, msb);//send pitchbend message
delay(10);
}
MIDImessage(noteON, note, 0);//turn note off delay(500);//wait 200ms until triggering next note }

//send MIDI message
void MIDImessage(int command, int data1, int data2) { Serial.write(command);//send command byte Serial.write(data1);//send data byte #1 Serial.write(data2);//send data byte #2
}

Below is a video demonstration of the code above. For this piece of code, pitchbend will be most noticeable in instruments with a long sustain, such as a string instrument, keep that in mind when testing the code for yourself.

You will most likely be fine using only 128 steps of pitchbend resolution, but in case you must use all 16384 steps, see the code below. Basically what I've done here is defined a variable called pitchbendVal, which varies from 0 to 16383. As I said below the "zero" pitchbend value is msb = 64 and lsb = 0. In binary this is:

## MSB = 64 = 01000000 LSB = 0 = 0000000 (remember MSB and LSB are 7 bit numbers)

## putting these values together we get:

1000000 0000000

## MSB LSB

or

10000000000000

## which translates to 8192 in decimal

so now the "zero" pitchbend value is 8192.

You'll also notice I had to break the variable pitchbendVal into two 7 bit parts to send out via MIDI message: MIDImessage(pitchbend, (pitchbendVal&27), (pitchbendVal>>7));

## the first part, pitchbendVal&127, returns the least significant 7 bits of pitchbendVal the second part, pitchbendVal>>7, returns the most significant 7 bits of pitchbendVal

see & (http://arduino.cc/en/Reference/BitwiseAnd) and >> (http://arduino.cc/en/Reference/Bitshift) on the Arduino reference page for more info.

/*
MIDI Pitchbend (full resolution)
By Amanda Ghassaei
July 2012
http://www.instructables.com/id/Send-and-Receive-MIDI-with-Arduino/

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

*/

int noteON = 144;//144 = 1001000 in binary, note on command
//noteON data storage:
int note = 60;//middle c
int velocity = 100;//velocity of MIDI notes, must be between 0 and 127 //(higher velocity usually makes MIDI instruments louder)

int pitchbend = 224;//224 = 11100000 in binary, pitchbend command //pitchbend data storage:
int pitchbendVal = 8192;//value between 0 and 16383. zero pitchbend = 8192

void setup() {
// Set MIDI baud rate:
Serial.begin(31250);
}

void loop() {
//first play note w/o pitchbend
pitchbendVal = 8192;//reset pitchbend to "0" (zero pitchbend is pitchbendVal = 8192) MIDImessage(pitchbend, (pitchbendVal&27), (pitchbendVal>>7));//send pitchbend message MIDImessage(noteON, note, velocity);//turn note on
delay(700);//sustain note
MIDImessage(noteON, note, 0);//turn note off
delay(500);//wait 500ms until triggering next note

//then play with pitchbend up
pitchbendVal = 8192;//reset pitchbend to "0" (zero pitchbend is pitchbendVal = 8192) MIDImessage(pitchbend, (pitchbendVal&27), (pitchbendVal>>7));//send pitchbend message MIDImessage(noteON, note, velocity);//turn note on
for (pitchbendVal=8192;pitchbendVal<16384;pitchbendVal++){//increase pitchbend from 8192 to 16383 MIDImessage(pitchbend, (pitchbendVal&27), (pitchbendVal>>7));//send pitchbend message delay(1);
}
MIDImessage(noteON, note, 0);//turn note off
delay(500);//wait 500ms until triggering next note

//then play with pitchbend down
pitchbendVal = 8192;//reset pitchbend to "0" (zero pitchbend is pitchbendVal = 8192) MIDImessage(pitchbend, (pitchbendVal&27), (pitchbendVal>>7));//send pitchbend message MIDImessage(noteON, note, velocity);//turn note on
for (pitchbendVal=8192;pitchbendVal>=0;pitchbendVal--){//decrease pitchbend 8192 to 0; MIDImessage(pitchbend, (pitchbendVal&27), (pitchbendVal>>7));//send pitchbend message delay(1);
}
MIDImessage(noteON, note, 0);//turn note off
delay(500);//wait 500ms until triggering next note }

//send MIDI message
void MIDImessage(int command, int data1, int data2) { Serial.write(command);//send command byte Serial.write(data1);//send data byte #1 Serial.write(data2);//send data byte #2
}

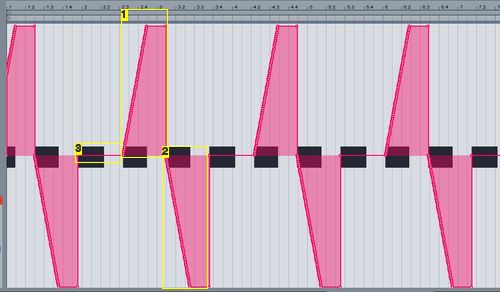
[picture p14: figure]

## Image Notes 1. pitchbend increments up from 0 to max 2. pitchbend increments down from 0 to min 3. constant pitchbend of 64 = no pitchbend

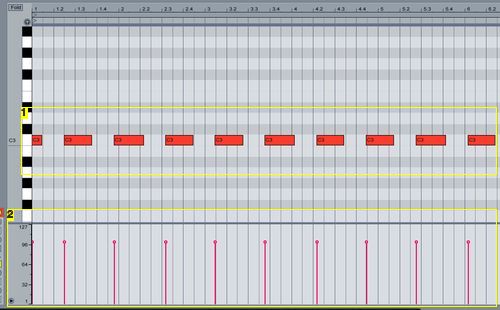
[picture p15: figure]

## Image Notes 1. same note (middle c) repeated over and over 2. constant velocity

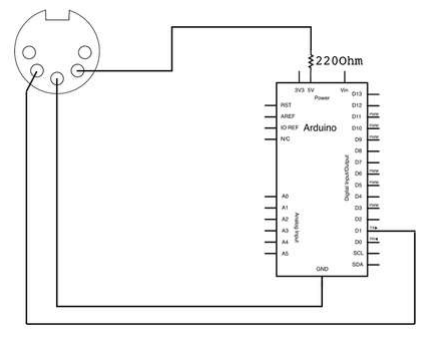
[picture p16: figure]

# Step 9: Receive MIDI Messages with Arduino

Most Arduino MIDI projects send MIDI messages out, but you can also use the Arduino to receive MIDI data. Here are some ideas:

## an Arduino synthesizer that uses MIDI messages to construct audio waveforms

a device which uses MIDI to trigger mechanical events, like the ringing of different sized bells

## a MIDI to control voltage(CV) device- communication between MIDI and analog synthesizers

## Parts List:

MIDI connector Digikey CP-2350-ND (http://www.digikey.com/product-detail/en/SDS-50J/CP-2350-ND/97033)
220Ohm 1/4watt resistor Digikey CF14JT220RCT-ND (http://www.digikey.com/product-detail/en/CF14JT220R/CF14JT220RCT-ND/1830334)
1N4148 diode Digikey1N4148-TAPCT-ND (http://www.digikey.com/product-detail/en/1N4148-TAP/1N4148-TAPCT-ND/3104296)
10kOhm 1/4watt resistor Digikey CF14JT10K0CT-ND (http://www.digikey.com/product-detail/en/CF14JT10K0/CF14JT10K0CT-ND/1830374)
470 Ohm 1/4watt resistor Digikey CF14JT470RCT-ND (http://www.digikey.com/product-detail/en/CF14JT470R/CF14JT470RCT-ND/1830342) (I used 2x220 instead)
6N138 optocoupler Digikey 751-1263-5-ND (http://www.digikey.com/product-detail/en/6N138/751-1263-5-ND/1731496)

The hardware setup is slightly more complicated for receiving MIDI than it is for sending. As you can see in the schematic above, you have to set up an optoisolator in between the MIDI jack and the Arduino. If you are confused about the MIDI pin connections, refer to fig 1. I set this circuit up on a breadboard in figs 4 and 5.

The following code receives these messages, reads them, and stores them appropriately. See the comments for more information.

/*Receive Midi
By Amanda Ghassaei
July 2012
http://www.instructables.com/id/Send-and-Receive-MIDI-with-Arduino/

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

*/

byte commandByte;
byte noteByte;
byte velocityByte;

void setup(){
Serial.begin(31250);
}

void checkMIDI(){
do{
if (Serial.available()){
commandByte = Serial.read();//read first byte noteByte = Serial.read();//read next byte velocityByte = Serial.read();//read final byte
}
}
while (Serial.available() > 24);//when three bytes available }

void loop(){
checkMIDI();
}
To make sure that everything is working properly, try the code below. This code turns the led at pin 13 on briefly when it receives a note on message for MIDI note 60 (middle C). Notice how I included "& velocityByte>0" in the if statement- this makes sure that we are dealing with a note on statement, if you don't include this the light will blink for both note on and note on with velocity = 0 (note off) messages.

/*Receive MIDI and check if note = 60
By Amanda Ghassaei
July 2012

* This program is free software; you can redistribute it and/or modify

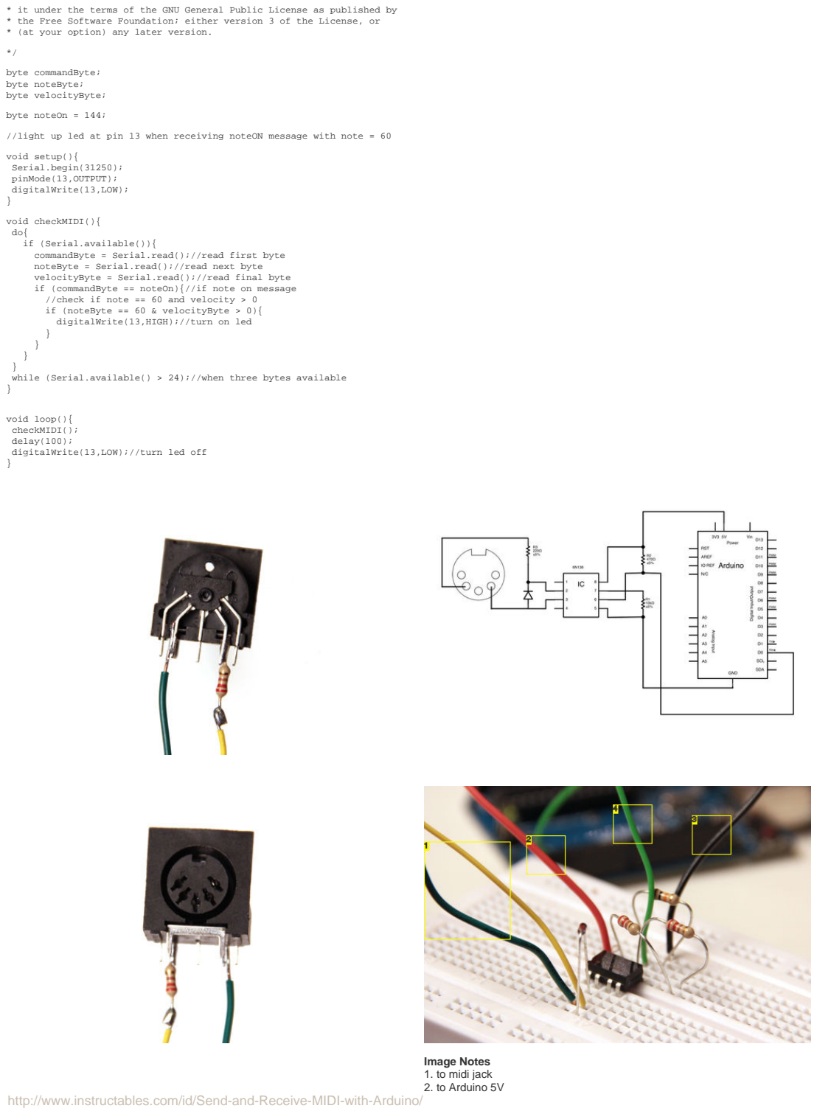
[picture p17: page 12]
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

*/

byte commandByte;
byte noteByte;
byte velocityByte;

byte noteOn = 144;

//light up led at pin 13 when receiving noteON message with note = 60

void setup(){
Serial.begin(31250);
pinMode(13,OUTPUT);
digitalWrite(13,LOW);
}

void checkMIDI(){
do{
if (Serial.available()){
commandByte = Serial.read();//read first byte noteByte = Serial.read();//read next byte velocityByte = Serial.read();//read final byte if (commandByte == noteOn){//if note on message //check if note == 60 and velocity > 0
if (noteByte == 60 & velocityByte > 0){ digitalWrite(13,HIGH);//turn on led
}
}
}
}
while (Serial.available() > 24);//when three bytes available }

void loop(){
checkMIDI();
delay(100);
digitalWrite(13,LOW);//turn led off }

## Image Notes 1. to midi jack 2. to Arduino 5V

## 3. to Arduino ground 4. to RX (digital pin 0)

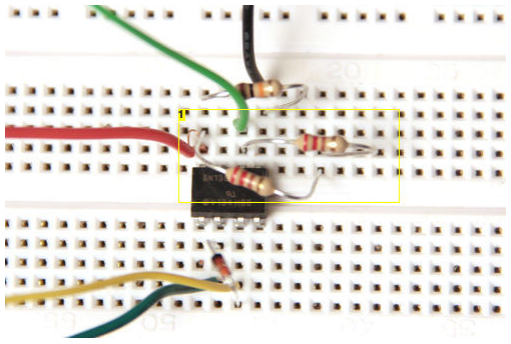
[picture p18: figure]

## Image Notes

1. I used two 220ohm resistors instead of one 470ohm.

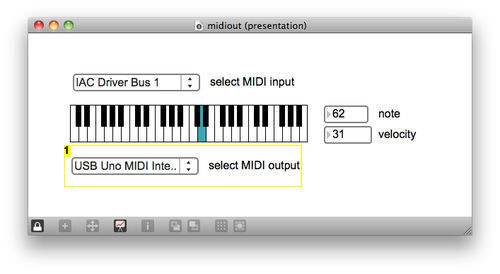
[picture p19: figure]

## Image Notes 1. select Arduino here

## File Downloads

midiout.maxpat.zip (http://www.instructables.com/files/orig/FJ9/A58S/H6DWVEBU/FJ9A58SH6DWVEBU.zip) (1 KB)
[NOTE: When saving, if you see .tmp as the file ext, rename it to 'midiout.maxpat.zip'] (http://www.instructables.com/files/orig/FJ9/A58S/H6DWVEBU/FJ9A58SH6DWVEBU.zip)

# Step 10: Examples

I recently built a MIDI controller with a built in accelerometer and gyroscope (http://www.instructables.com/id/Use-an-Accelerometer-and-Gyroscope-with-Arduino/) , as well as 16 backlit buttons. I'll be posting the full project soon (still need to finish enclosure and a few other things), but I've attached some example code that shows how I got the MIDI up and running. Here is a video of two programs I've written so far:

## And here is the code for those applications:

## single pixel moving around, triggering MIDI (only uses x and y accelerometer):

//accelerometer test- single pixel
//by Amanda Ghassaei 2012
//http://www.instructables.com/id/Send-and-Receive-MIDI-with-Arduino/

/*
* This program is free software; you can redistribute it and/or modify * it under the terms of the GNU General Public License as published by * the Free Software Foundation; either version 2 of the License, or * (at your option) any later version.
*
*/

//pin connections
//#define ledLatchPin 6
//#define ledClockPin 5
//#define ledDataPin 7
//#define buttonLatchPin 4
//#define buttonClockPin 3
//#define buttonDataPin 2

//setup varibles for Gyroscope/Accelerometer int xGyroRAW;
int yGyroRAW;
int xAccRAW;
int yAccRAW;
int zAccRAW;

byte xGyro;
byte yGyro;
byte xAcc;
byte yAcc;
byte zAcc;

//looping variables
byte i;
byte j;
byte k;

//storage for led states, 4 bytes byte ledData[] = {0, 0, 0, 0}; //storage for buttons, 4 bytes byte buttonCurrent[] = {0,0,0,0}; byte buttonLast[] = {0,0,0,0};

byte buttonEvent[] = {0,0,0,0}; byte buttonState[] = {0,0,0,0};
//button debounce counter- 16 bytes
byte buttonDebounceCounter[4][4];

//variables for accelerometer pixel movement boolean firstPress = 1;
byte movingPixel[] = {0, 0, 0, 0};
byte yPosition;
byte xPosition;
int timeX = 0;
int timeY = 0;
boolean dirX = 0;
boolean dirY = 0;
byte lastX = 4;
byte lastY = 4;

//MIDI variables
int velocity = 100;
int noteON = 144;
int MIDIoffset = 60;
byte currentX;

void setup() {

DDRD = 0xFA;//set pins D7-D4 as output, D2 as input

Serial.begin(31250);//MIDI baud rate
// Serial.begin(9600);

cli();//stop interrupts

//set timer1 interrupt at 1kHz
TCCR1A = 0;// set entire TCCR1A register to 0 TCCR1B = 0;// same for TCCR1B
TCNT1 = 0;//initialize counter value to 0; // set timer count for 1khz increments
OCR1A = 1999;// = (16*10^6) / (1000*8) - 1 // turn on CTC mode
TCCR1B |= (1 << WGM12);
// Set CS11 bit for 8 prescaler
TCCR1B |= (1 << CS11);
// enable timer compare interrupt TIMSK1 |= (1 << OCIE1A);

sei();//allow interrupts

}

ISR(TIMER1_COMPA_vect) {//Interrupt at freq of 1kHz timeX++;//increment timeX
timeY++;//increment timeY
shift();//send data to leds
}

// buttonCheck - checks the state of a given button.
//this buttoncheck function is largely copied from the monome 40h firmware by brian crabtree and joe lake
void buttonCheck(byte row, byte index)
{
if (((buttonCurrent[row] ^ buttonLast[row]) &(1 << index)) && // if the current physical button state is different from the ((buttonCurrent[row] ^ buttonState[row]) &(1 << index))) { // last physical button state AND the current debounced state
if (buttonCurrent[row] &(1 << index)) { | // if the current physical button state is depressed
buttonEvent[row] = 1 << index; | // queue up a new button event immediately
buttonState[row] |= (1 << index); | // and set the debounced state to down.
}
else{
buttonDebounceCounter[row][index] = 12;
} // otherwise the button was previously depressed and now
// has been released so we set our debounce counter.
}
else if (((buttonCurrent[row] ^ buttonLast[row]) &(1 << index)) == 0 && // if the current physical button state is the same as
(buttonCurrent[row] ^ buttonState[row]) &(1 << index)) { | // the last physical button state but the current physical
// button state is different from the current debounce
// state...
if (buttonDebounceCounter[row][index] > 0 && --buttonDebounceCounter[row][index] == 0) { // if the the debounce counter has // been decremented to 0 (meaning the
// the button has been up for
// kButtonUpDefaultDebounceCount
// iterations///
buttonEvent[row] = 1 << index; | // queue up a button state change event
if (buttonCurrent[row] &(1 << index)){ | // and toggle the buttons debounce state.
buttonState[row] |= (1 << index);
}
else{
buttonState[row] & ~(1 << index); }
}
}
}

void shift(){

for (i=0;i<4;i++){

buttonLast[i] = buttonCurrent[i];

byte dataToSend = (1 << (i+4)) | (15 &~ledData[i]);

// set latch pin low so the LEDs don't change while sending in bits PORTD&B10111111;//digitalWrite(ledLatchPin, LOW);
// shift out the bits of dataToSend
//shiftOut(ledDataPin, ledClockPin, LSBFIRST, dataToSend);
for (j=0;j<8;j++){
PORTD&B11011111;//digitalWrite(ledClockPin,LOW); //digitalWrite(ledDataPin,((dataToSend>>j)&));
if ((dataToSend>>j)&1){
PORTD|=B10000000;
}
else{
PORTD&B01111111;
}
PORTD|=B00100000;//digitalWrite(ledClockPin,HIGH); }
//set latch pin high so the LEDs will receive new data PORTD|=B01000000;//digitalWrite(ledLatchPin, HIGH);

// SlowDown is put in here to waste a little time while we wait for the state of the output // pins to settle. Without this time wasting loop, a single button press would show up as // two presses (the button and its neighbour)
volatile int SlowDown = 0;

while (SlowDown < 15)
{
SlowDown++;
}

//once one row has been set high, receive data from buttons //set latch pin high
PORTD|=B00010000;//digitalWrite(buttonLatchPin, HIGH);
//shift in data
//buttonCurrent[i] = shiftIn(buttonDataPin, buttonClockPin, LSBFIRST) >> 3; for (j=0;j<4;j++){
PORTD&B11110111;//digitalWrite(buttonClockPin,LOW); PORTD|=B00001000;//digitalWrite(buttonClockPin,HIGH);
}
for (j=0;j<4;j++){
PORTD&B11110111;//digitalWrite(buttonClockPin,LOW); if ((PIND>>2)&1){//digitalRead(buttonDataPin) buttonCurrent[i]|=1<<j;
}
else{
buttonCurrent[i]&~(1<<j);
}
PORTD|=B00001000;//digitalWrite(buttonClockPin,HIGH); }
//latchpin low
PORTD&B11101111;//digitalWrite(buttonLatchPin, LOW);

for (k=0;k<4;k++){
buttonCheck(i,k);
}
}

//turn off leds- this way one row does not appear brighter than the rest

// set latch pin low so the LEDs don't change while sending in bits PORTD&B10111111;//digitalWrite(ledLatchPin, LOW);
// shift out 0
//shiftOut(ledDataPin, ledClockPin, LSBFIRST, 0);
for (j=0;j<8;j++){
PORTD&B11011111;//digitalWrite(ledClockPin,LOW); PORTD&B01111111;
PORTD|=B00100000;//digitalWrite(ledClockPin,HIGH); }
//set latch pin high so the LEDs will receive new data PORTD|=B01000000;//digitalWrite(ledLatchPin, HIGH);
}

void checkFirstButton(){
for (byte a=0;a<4;a++){
if (buttonEvent[a]){
for (byte b=0;b<4;b++){
if (buttonState[a]&1<<b)){ //toggle firstPress variable firstPress = 0;
//display pressed pixel
ledData[a] = buttonEvent[a]; //store current position
yPosition = a;
xPosition = 1<<b;
//reset timers
timeX = 0;
timeY = 0;
return;
}
}
}
}
}

byte scaleAcc(int RAW){
if (RAW<=10 & RAW>=-10){
return 5;

else if (RAW<-10){
if (RAW<-50){
return 0;

else if (RAW<-40){
return 1;
}
else if (RAW<-30){
return 2;
}
else if (RAW<-20){
return 3;
}
else{
return 4;
}
}
else if (RAW>10){
if (RAW>50){
return 10;
}
else if (RAW>40){
return 9;
}
else if (RAW>30){
return 8;
}
else if (RAW>20){
return 7;
}
else{
return 6;
}
}
}

void checkAccelerometer(){ //read values
xGyroRAW = analogRead(A1); yGyroRAW = analogRead(A0); xAccRAW = analogRead(A4);
yAccRAW = analogRead(A3);
zAccRAW = analogRead(A2);

//offset data
xGyroRAW = 317-xGyroRAW;
yGyroRAW = 183-yGyroRAW;
xAccRAW = 282-xAccRAW;
yAccRAW = 282-yAccRAW;
zAccRAW = 282-zAccRAW;

if (xAccRAW>0){
dirX = 1;
}
else{
dirX = 0;
}
if (yAccRAW>0){
dirY = 1;
}
else{
dirY = 0;
}

//convert to 0-10
xAcc = scaleAcc(xAccRAW);
yAcc = scaleAcc(yAccRAW);
}

int getTime(byte acceleration){ switch (acceleration){
case 0://max - acceleration return 25;
break;
case 1:
return 25;
break;
case 2:
return 50;
break;
case 3:
return 100;
break;
case 4:
return 150;
break;
case 5://lying flat
return 0;
break;
case 6:
return 150;
break;
case 7:
return 100;
break;
case 8:
return 50;
break;

case 9:
return 25;
break;
case 10://max + acceleration return 25;
break;
}
}

void moveXPixel(int timeComp){ if (timeComp==0){
}
else{
if (timeX>timeComp){
timeX = 0;
if (dirX){
if (xPosition==8){
}
else{
xPosition = xPosition<<1;
}
}
else{
if (xPosition==1){
}
else{
xPosition = xPosition>>1;
}
}
}
}
}

void moveYPixel(int timeComp){ if (timeComp==0){
}
else{
if (timeY>timeComp){
timeY = 0;
if (dirY){
if (yPosition==3){
}
else{
yPosition = yPosition+=1;
}
}
else{
if (yPosition==0){
}
else{
yPosition = yPosition-=1;
}
}
}
}
}

void checkMIDI(){
//convert xPosition to decimal switch (xPosition){
case 1:
currentX = 0;
break;
case 2:
currentX = 1;
break;
case 4:
currentX = 2;
break;
case 8:
currentX = 3;
break;
}
//if pixel has moved send midi
if (lastX != currentX || lastY != yPosition){ MIDImessage(noteON,(lastX+5*lastY+MIDIoffset),0);//turn off last note MIDImessage(noteON,(currentX+5*yPosition+MIDIoffset),velocity);//turn on next note }
lastX = currentX;
lastY = yPosition;
}

void MIDImessage(int command, int MIDInote, int MIDIvelocity) {//send s a MIDI message Serial.write(command);//send note on or note off command Serial.write(MIDInote);//send pitch data
Serial.write(MIDIvelocity);//send velocity data
}

void loop() {
if (firstPress){
checkFirstButton();
}
else{
for (byte pixel=0;pixel<4;pixel++){ if (pixel==yPosition){
ledData[pixel]=xPosition;

else{
ledData[pixel] = 0;

checkAccelerometer();
moveXPixel(getTime(xAcc)); moveYPixel(getTime(yAcc)); checkMIDI();
}
}

## four pixels bouncing (only uses x accelerometer, uses x gyro to clear pixels):

//accelerometer test- bounce
//by Amanda Ghassaei 2012
//http://www.instructables.com/id/Send-and-Receive-MIDI-with-Arduino/

/*
* This program is free software; you can redistribute it and/or modify * it under the terms of the GNU General Public License as published by * the Free Software Foundation; either version 2 of the License, or * (at your option) any later version.
*
*/

//pin connections
//#define ledLatchPin 6
//#define ledClockPin 5
//#define ledDataPin 7
//#define buttonLatchPin 4
//#define buttonClockPin 3
//#define buttonDataPin 2

//setup varibles for Gyroscope/Accelerometer int xGyroRAW;
int yGyroRAW;
int xAccRAW;
int yAccRAW;
int zAccRAW;

byte xGyro;
byte yGyro;
byte xAcc;
byte yAcc;
byte zAcc;

//looping variables
byte i;
byte j;
byte k;

//storage for led states, 4 bytes byte ledData[] = {0, 0, 0, 0}; //storage for buttons, 4 bytes byte buttonCurrent[] = {0,0,0,0}; byte buttonLast[] = {0,0,0,0}; byte buttonEvent[] = {0,0,0,0}; byte buttonState[] = {0,0,0,0};
//button debounce counter- 16 bytes
byte buttonDebounceCounter[4][4];

//variables for accelerometer pixel movement boolean firstPress[] = {0, 0, 0, 0};
byte movingPixel[] = {0, 0, 0, 0};
byte xPosition[4];
int timeX[] = {0, 0, 0, 0}; boolean dirX;
boolean dirY;
boolean prevDirX = 0;
boolean bounceDirection[]= {0, 0, 0, 0}; boolean toggle[] = {1, 1, 1, 1};
byte peakHeight[4];
byte lastX = 4;
byte lastY = 4;

//MIDI variables
int velocity = 100;
int noteON = 144;
int MIDIoffset = 60;
byte currentX;
byte note[] = {60, 64, 67, 72};

void setup() {

DDRD = 0xFA;//set pins D7-D4 as output, D2 as input

Serial.begin(31250);//MIDI baud rate

cli();//stop interrupts

//set timer1 interrupt at 1kHz
TCCR1A = 0;// set entire TCCR1A register to 0 TCCR1B = 0;// same for TCCR1B
TCNT1 = 0;//initialize counter value to 0; // set timer count for 1khz increments
OCR1A = 1999;// = (16*10^6) / (1000*8) - 1

// turn on CTC mode
TCCR1B |= (1 << WGM12);
// Set CS11 bit for 8 prescaler TCCR1B |= (1 << CS11);
// enable timer compare interrupt TIMSK1 |= (1 << OCIE1A);

sei();//allow interrupts

}

ISR(TIMER1_COMPA_vect) {//Interrupt at freq of 1kHz for (byte a=0;a<4;a++){
timeX[a]++;//increment each element of timeX
}
shift();
}

// buttonCheck - checks the state of a given button.
//this buttoncheck function is largely copied from the monome 40h firmware by brian crabtree and joe lake
void buttonCheck(byte row, byte index)
{
if (((buttonCurrent[row] ^ buttonLast[row]) &(1 << index)) && // if the current physical button state is different from the ((buttonCurrent[row] ^ buttonState[row]) &(1 << index))) { // last physical button state AND the current debounced state
if (buttonCurrent[row] &(1 << index)) { | // if the current physical button state is depressed
buttonEvent[row] = 1 << index; | // queue up a new button event immediately
buttonState[row] |= (1 << index); | // and set the debounced state to down.
}
else{
buttonDebounceCounter[row][index] = 12;
} // otherwise the button was previously depressed and now
// has been released so we set our debounce counter.
}
else if (((buttonCurrent[row] ^ buttonLast[row]) &(1 << index)) == 0 && // if the current physical button state is the same as
(buttonCurrent[row] ^ buttonState[row]) &(1 << index)) { | // the last physical button state but the current physical
// button state is different from the current debounce
// state...
if (buttonDebounceCounter[row][index] > 0 && --buttonDebounceCounter[row][index] == 0) { // if the the debounce counter has // been decremented to 0 (meaning the
// the button has been up for
// kButtonUpDefaultDebounceCount
// iterations///
buttonEvent[row] = 1 << index; | // queue up a button state change event
if (buttonCurrent[row] &(1 << index)){ | // and toggle the buttons debounce state.
buttonState[row] |= (1 << index);
}
else{
buttonState[row] & ~(1 << index); }
}
}
}

void shift(){

for (i=0;i<4;i++){

buttonLast[i] = buttonCurrent[i];

byte dataToSend = (1 << (i+4)) | (15 &~ledData[i]);

// set latch pin low so the LEDs don't change while sending in bits PORTD&B10111111;//digitalWrite(ledLatchPin, LOW);
// shift out the bits of dataToSend
//shiftOut(ledDataPin, ledClockPin, LSBFIRST, dataToSend);
for (j=0;j<8;j++){
PORTD&B11011111;//digitalWrite(ledClockPin,LOW); //digitalWrite(ledDataPin,((dataToSend>>j)&));
if ((dataToSend>>j)&1){
PORTD|=B10000000;
}
else{
PORTD&B01111111;
}
PORTD|=B00100000;//digitalWrite(ledClockPin,HIGH); }
//set latch pin high so the LEDs will receive new data PORTD|=B01000000;//digitalWrite(ledLatchPin, HIGH);

// SlowDown is put in here to waste a little time while we wait for the state of the output // pins to settle. Without this time wasting loop, a single button press would show up as // two presses (the button and its neighbour)
volatile int SlowDown = 0;

while (SlowDown < 15)
{
SlowDown++;
}

//once one row has been set high, receive data from buttons //set latch pin high
PORTD|=B00010000;//digitalWrite(buttonLatchPin, HIGH);
//shift in data
//buttonCurrent[i] = shiftIn(buttonDataPin, buttonClockPin, LSBFIRST) >> 3; for (j=0;j<4;j++){
PORTD&B11110111;//digitalWrite(buttonClockPin,LOW);

PORTD|=B00001000;//digitalWrite(buttonClockPin,HIGH);

for (j=0;j<4;j++){
PORTD&B11110111;//digitalWrite(buttonClockPin,LOW); if ((PIND>>2)&1){//digitalRead(buttonDataPin) buttonCurrent[i]|=1<<j;
}
else{
buttonCurrent[i]&~(1<<j);
}
PORTD|=B00001000;//digitalWrite(buttonClockPin,HIGH); }
//latchpin low
PORTD&B11101111;//digitalWrite(buttonLatchPin, LOW);

for (k=0;k<4;k++){
buttonCheck(i,k);
}
}

//turn off leds- this way one row does not appear brighter than the rest

// set latch pin low so the LEDs don't change while sending in bits PORTD&B10111111;//digitalWrite(ledLatchPin, LOW);
// shift out 0
//shiftOut(ledDataPin, ledClockPin, LSBFIRST, 0);
for (j=0;j<8;j++){
PORTD&B11011111;//digitalWrite(ledClockPin,LOW); PORTD&B01111111;
PORTD|=B00100000;//digitalWrite(ledClockPin,HIGH); }
//set latch pin high so the LEDs will receive new data PORTD|=B01000000;//digitalWrite(ledLatchPin, HIGH);
}

void checkPress(byte Y){
if (buttonEvent[Y]){
for (byte b=0;b<4;b++){
if (buttonState[Y]&1<<b)){ //toggle firstPress variable firstPress[Y] = 1;
//display pressed pixel
ledData[Y] = (1<<b);
//store current position
xPosition[Y] = (1<<b);
//store peak height
peakHeight[Y] = (1<<b);
//reset timers
timeX[Y] = 0;
return;
}
}
}
}

byte scaleAcc(int RAW){
if (RAW<=10 & RAW>=-10){
return 5;
}
else if (RAW<-10){
if (RAW<-50){
return 0;
}
else if (RAW<-40){
return 1;
}
else if (RAW<-30){
return 2;
}
else if (RAW<-20){
return 3;
}
else{
return 4;
}
}
else if (RAW>10){
if (RAW>50){
return 10;
}
else if (RAW>40){
return 9;
}
else if (RAW>30){
return 8;
}
else if (RAW>20){
return 7;
}
else{
return 6;
}
}
}

void checkAccelerometerGyro(){ //read values
xGyroRAW = analogRead(A1);

yGyroRAW = analogRead(A0); xAccRAW = analogRead(A4);
yAccRAW = analogRead(A3);
zAccRAW = analogRead(A2);

//offset data
xGyroRAW = 317-xGyroRAW;
yGyroRAW = 183-yGyroRAW;
xAccRAW = 282-xAccRAW;
yAccRAW = 282-yAccRAW;
zAccRAW = 282-zAccRAW;

//convert to 0-10
xAcc = scaleAcc(xAccRAW);
yAcc = scaleAcc(yAccRAW);

if (xAccRAW>5){
dirX = 1;
}
else if (xAccRAW<5){
dirX = 0;
}
if (yAccRAW>5){
dirY = 1;
}
else if (yAccRAW>5){
dirY = 0;
}

}

int getTime(byte acceleration){ switch (acceleration){
case 0://max - acceleration return 100;
break;
case 1:
return 100;
break;
case 2:
return 150;
break;
case 3:
return 200;
break;
case 4:
return 250;
break;
case 5://lying flat
return 0;
break;
case 6:
return 250;
break;
case 7:
return 200;
break;
case 8:
return 150;
break;
case 9:
return 100;
break;
case 10://max + acceleration return 100;
break;
}
}

void moveXPixel(byte Y, int timeComp){ if (timeComp==0){
}
else{
if (timeX[Y]>timeComp){
timeX[Y] = 0;
if (dirX){
if (peakHeight[Y]==8&&xPosition[Y]==8){ if(toggle[Y]){
MIDImessage(noteON,note[Y],0);//send midi toggle[Y]=0;
ledData[Y]=0;
}
else{
MIDImessage(noteON,note[Y],velocity); toggle[Y]=1;
}
}
else{
toggle[Y]=1;
if (xPosition[Y]==peakHeight[Y]){//if at peak bounceDirection[Y]=1;//falling MIDImessage(noteON,note[Y],0);//turn note off }
if (xPosition[Y]==8){//if hitting bottom bounceDirection[Y]=0;//rising MIDImessage(noteON,note[Y],velocity);//turn note on

if (xPosition[Y]==1){

bounceDirection[Y]=1;

if (bounceDirection[Y]){
xPosition[Y] = xPosition[Y]<<1;

else{
xPosition[Y] = xPosition[Y]>>1; }
}
}
else{
if (peakHeight[Y]==1&&xPosition[Y]==1){ if(toggle[Y]){
MIDImessage(noteON,note[Y],0);//send midi toggle[Y]=0;
ledData[Y]=0;
}
else{
MIDImessage(noteON,note[Y],velocity); toggle[Y]=1;
}
}
else{
toggle[Y]=1;
if (xPosition[Y]==peakHeight[Y]){//if at peak bounceDirection[Y]=0;//falling MIDImessage(noteON,note[Y],0);//turn note off }
if (xPosition[Y]==8){
bounceDirection[Y]=0;
}
if (xPosition[Y]==1){//if hitting bottom bounceDirection[Y]=1;//rising MIDImessage(noteON,note[Y],velocity);//turn note on }
if (bounceDirection[Y]){
xPosition[Y] = xPosition[Y]<<1;
}
else{
xPosition[Y] = xPosition[Y]>>1; }
}
}
}
}
}

void shake2Clear(){
if (abs(xGyroRAW)>300){
for (byte a=0;a<4;a++){
firstPress[a]=0;
ledData[a]=0;
}
}
}

void MIDImessage(int command, int MIDInote, int MIDIvelocity) {//send s a MIDI message Serial.write(command);//send note on or note off command Serial.write(MIDInote);//send pitch data
Serial.write(MIDIvelocity);//send velocity data
}

void loop() {
checkAccelerometerGyro();
shake2Clear();
for (byte column=0;column<4;column++){ checkPress(column);
if (firstPress[column]){
moveXPixel(column, getTime(xAcc)); if (toggle[column]){
ledData[column]= xPosition[column]; }
}
}
}

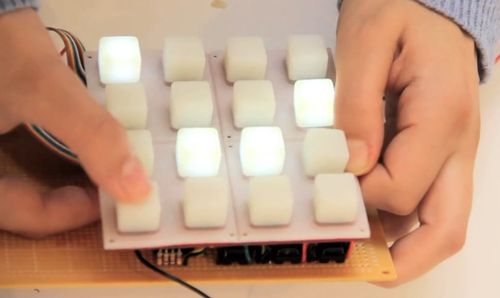
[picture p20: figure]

# Related Instructables

What is MIDI? (http://www.instructables.com/id/What-is-MIDI/?utm_source=pdf&utm_campaign=related)
by
amandaghassaei (http://www.instructables.com/member/amandaghassaei/?utm_source=pdf&utm_campaign=related)

## Converting a rescued toy into

a MIDI controller (http://www.instructables.com/id/Converting-a-rescued-toy-into-a-MIDI-controller/)
by zen.webb (http://www.instructables.com/member/zen.webb/?utm_source=pdf&utm_campaign=related)

## Portable MIDI Tone Generator On-the-Cheap (http://www.instructables.com/id/Portable-MIDI-Tone-Generator-On-the-Cheap/)

by lewisb42 (http://www.instructables.com/member/lewisb42/?utm_source=pdf&utm_campaign=related)

## Adding MIDI to Old Home

Organs (http://www.instructables.com/id/Adding-MIDI-to-Old-Home-Organs/?utm_source=pdf&utm_campaign=related) by

## uhclem (http://www.instructables.com/member/uhclem/?utm_source=pdf&utm_campaign=related)

## Electronic

Instrument (http://www.instructables.com/id/Electronic-Instrument/?utm_source=pdf&utm_campaign=related) by
amandaghassaei (http://www.instructables.com/member/amandaghassaei/?utm_source=pdf&utm_campaign=related)

## Arcade Button

MIDI Controller (http://www.instructables.com/id/Arcade-Button-MIDI-Controller/?utm_source=pdf&utm_campaign=related)
by fraganator (http://www.instructables.com/member/fraganator/?utm_source=pdf&utm_campaign=related)

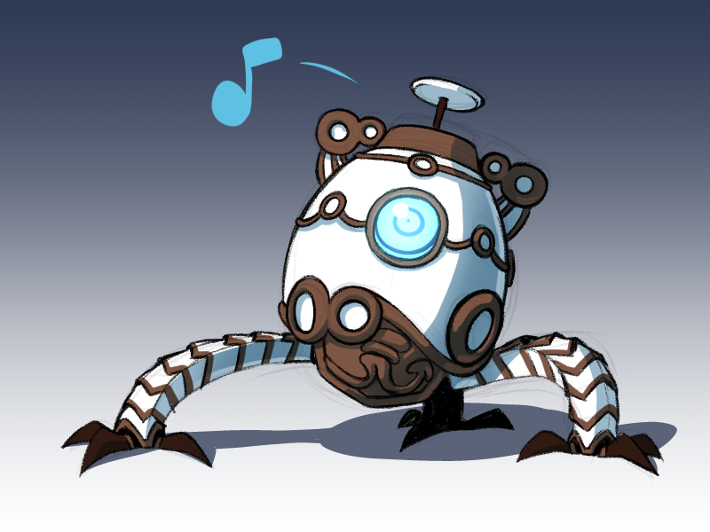
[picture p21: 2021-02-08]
Images/de98lke-fb39619d-336d-4663-add4-e0f87b19a37b.png

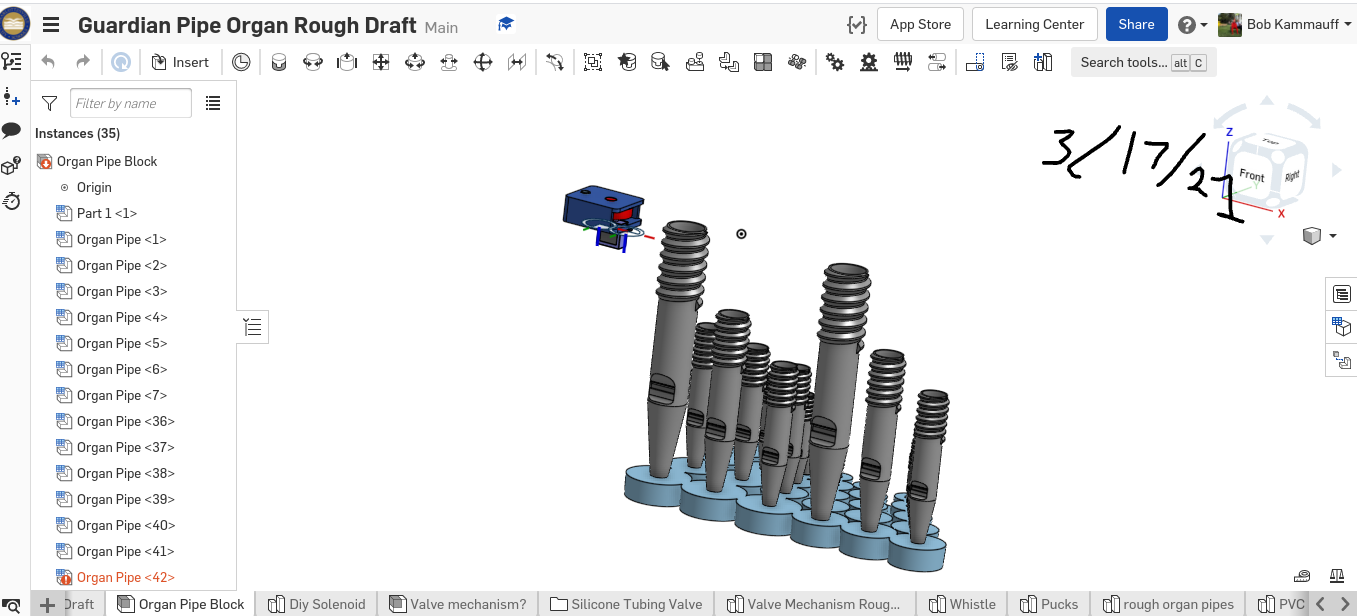
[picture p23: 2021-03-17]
Images/Screenshot 2021-03-17 2.41.42 PM.png

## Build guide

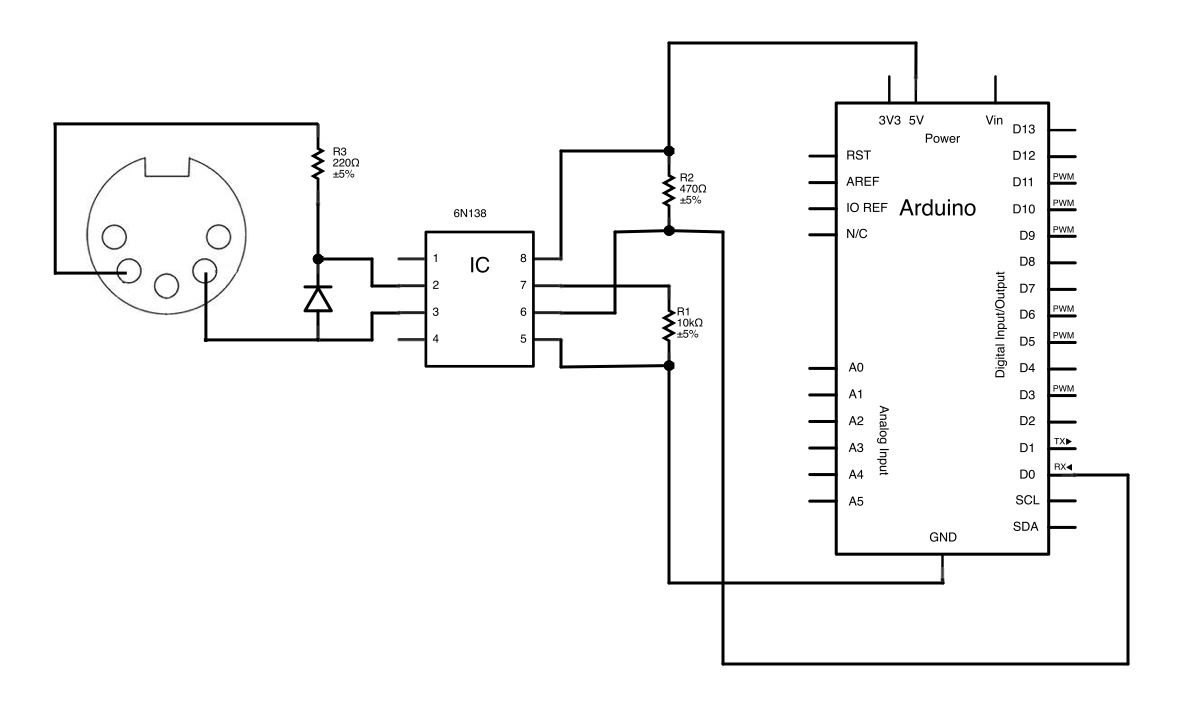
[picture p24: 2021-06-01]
Images/MidiWiring.jpg

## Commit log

2021-04-13 Finding basis for arduino midi code
2021-04-19 Can't figure out how to print stuff better
2021-05-11 uploaded code from arduino create
2021-05-17 Turning serial into servo commands until i get the midi cable
2021-05-17 Can Control servos via serial monitor
2021-05-25 got valve working
2021-05-26 Valve actually works
2021-06-01 wiring diagram
2021-06-01 Started on MIDI Code; Got arduino wired up
2021-06-07 Did wiring for midi
    [MidiCircuit.fzz, Opto-Isolator.fzz]
2021-06-11 Finished code part of readme; started cad oh boy
